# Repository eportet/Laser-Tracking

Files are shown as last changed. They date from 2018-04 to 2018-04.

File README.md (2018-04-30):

# Laser-Tracking

Code
====

Three folders in this directory:
* CameraTracking: Contains code that does corse tracking on RasPi
* Transmitter: Contains code that runs on photon plugged inito receiver PCBs
* Receiver: Contains code that runs on photon controlling servos and MEMS

Flashing Photon Code
====================

* Download Particle CLI on Mac or Linux. See Particle help for details.
* Place Photon in DFU mode by holding down both buttons, release Setup button. Light should blink purple, continue to hold the Reset button until light blinks yellow.
* Run ```particle photon compile --saveTo out.bin .``` in directory with *.ino file.
* Run ```particle flash --usb out.bin```
* When program is running, particle light should be constant white. If the light blinks green or blue, something is wrong, check that system mode is set to manual in code and that photon firmware is up to date.

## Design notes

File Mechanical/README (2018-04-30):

#Mechanical Components

Compatible with components ordered from:
[[https://www.amazon.com/gp/product/B00JXO9DBG/ref=oh_aui_detailpage_o03_s00?ie=UTF8&psc=1]]

MG995 Servos used.

Designed with Google Sketch Up.

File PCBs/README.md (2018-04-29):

# PCBs for laser tracking
We've got two PCBs to make the sensor for the drone.
The **sensor** board holds 24 photodiodes and sticks the info on a 26-pin header. The outputs require pullup resistors.
The **mux** board attaches to the sensor board, and is also designed to hold a particle photon and a RF communication module.

The kicad files, digikey bill of materials, and gerbers are in each of the directories. BOM for 3 boards + a spare, which is the minumum oshpark order.
We printed both boards with oshpark and it worked out well enough. "Sensor" is on 2oz copper, "mux" is standard.

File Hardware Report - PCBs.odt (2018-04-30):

Hardware Report

Hardware for our project includes two PCBs to be mounted on the drone. The source for these PCBs is stored in the repository, under “/PCBs/sensor” and “/PCBs/mux”.

1. Schematic files

PDFs of the circuit schematics are included in the repository, under:

1. /PCBs/sensor/sensor_sch1.pdf

2. /PCBs/sensor/sensor_sch2.pdf

3. /PCBs/mux/mux_sch1.pdf

The source files for these schematics, as well as the routed PCBs and gerber files, are included in the same directories.

2. Development Tools

We used kicad version 4.0.7 to construct these PCBs. Kicad is a free electronics design tool available on windows, mac, and linux. It can be obtained as a binary from:

http://kicad-pcb.org/

We used the standard schematic library obtained from

https://github.com/KiCad/kicad-library

The symbols for this library are intended to work with Kicad version 4.0.x. Kicad has since upgraded to version 5.0.x with new standard library components; these components are outside the scope of this document.

This library can be installed by cloning the repository, and then setting the search path to point to the cloned “/library” directory. The path can be set in:

kicad → library editor → preferences → user defined search path → add

3. Bill of materials

The bill of materials for each board is included as a CSV exported from digikey, under:

/PCBs/sensor/digikey_bom.csv

/PCBs/mux/digikey_bom.csv

Each of these BOMs represents the components needed for one board without spares. It is recommended that when you purchase components, you buy slightly more than necessary to account for damaged or lost components during manufacturing. The OSHPark minimum board order is three copies of a board; we generally ordered parts for four.

Datasheets for these parts are available from digikey.

4. Power

Our boards are designed for a 5-volt power source, which will also power the particle photon and the NRF24L01 module when they are connected. The five volt input should be connected to each board on the pins in positions marked with the red circle below. The adjacent pin is the ground pin.

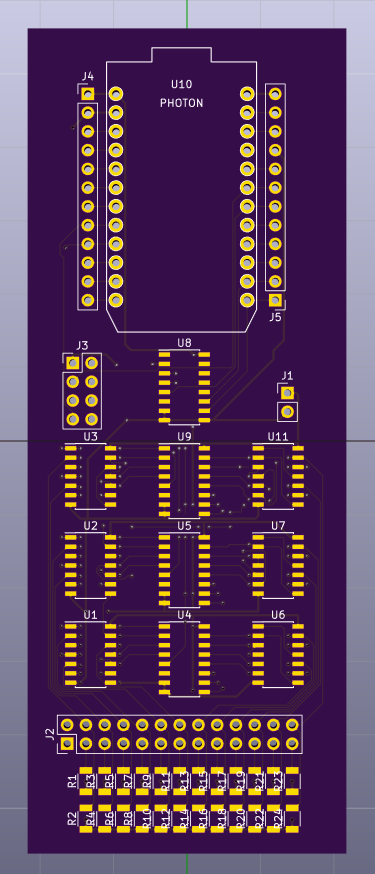
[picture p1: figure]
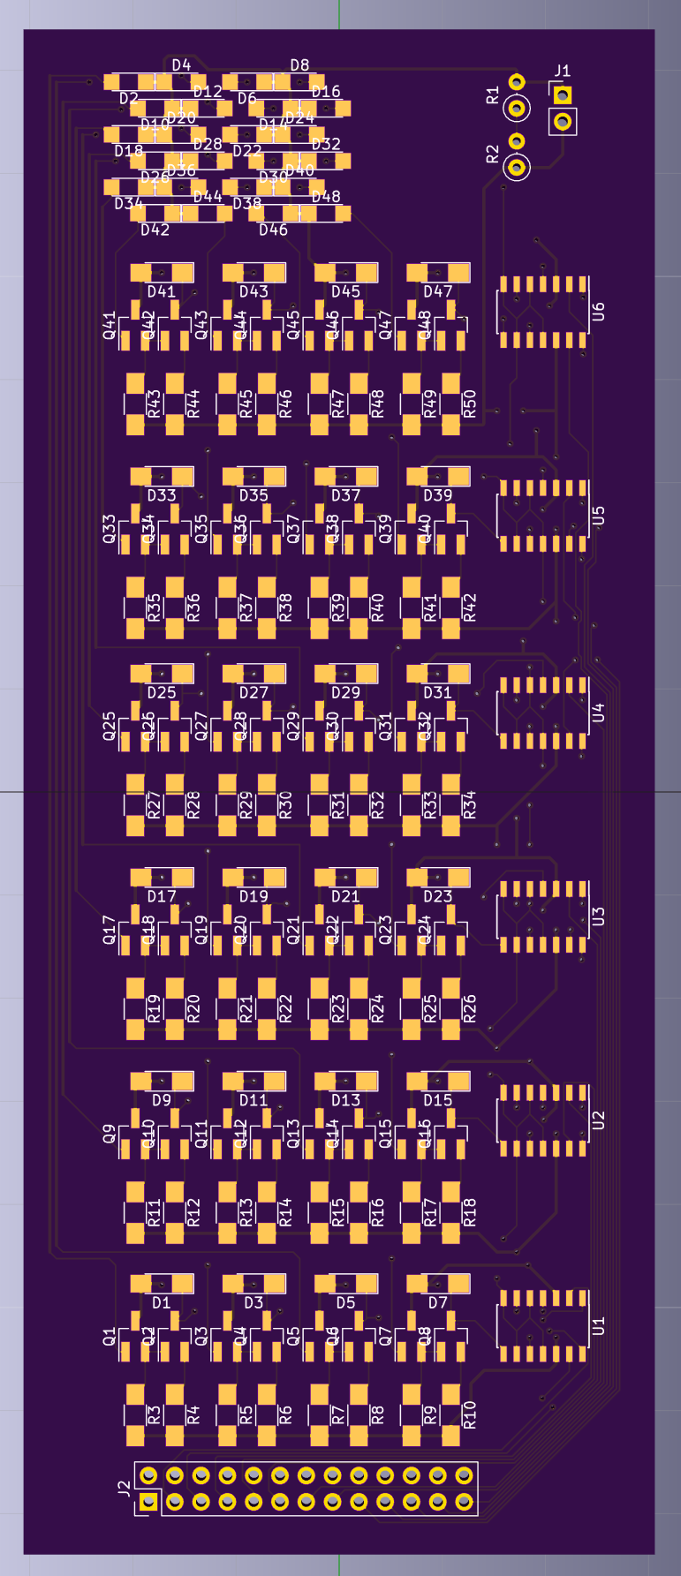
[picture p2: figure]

The “Sensor” board (left) has a resistor bridge next to the power input, designed to be filled with through-hole resistors. This bridge sets the sensitivity threshold of the photodiodes. The ratio of r2 / r1 should be about 3/2. Raising the value of r2 will decrease the sensitivity of the resistors, and lowering it will do the opposite.

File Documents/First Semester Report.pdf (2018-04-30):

## Boston University Electrical & Computer Engineering

EC 463 Capstone Senior Design Project

## First Semester Report

## UAV Laser Tracking

Submitted to

Professor Thomas Little, PhD 8 St. Mary’s St., Boston
MA 02215, Room 426
(617) 353-9877
tdcl@bu.edu

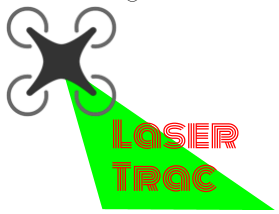
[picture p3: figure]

by Team 15
LaserTrac

Team Members
Aviva Englander | englanda@bu.edu
Christopher Liao | cliao25@bu.edu
Jeffrey Lin | jlin96@bu.edu
Anton Paquin | paquin@bu.edu
Eduardo Portet | eportet@bu.edu

Submitted: 12/11/2017

First Semester Report | 1

Table of Contents

Executive Summary | 2
1. | Introduction | 3
2. | Concept Development | 4
2.1. | Laser Steering Mechanism | 5
2.2. | Receiver | 6
2.3. | Tracking Algorithm | 7
2.4. | Backlink | 7
3. | System Description | 8
3.1. | Backwards Link | 8
3.2. | Primary Station Controller | 8
3.3. | Laser Controller | 9
3.4. | Data Controller and Laser | 9
3.5. | Photodiode Array | 9
3.6. | Motion Controls | 10
3.7. | Camera and Coarse Control | 10
4. | First Semester Progress | 11
5. | Technical Plan | 12
5.1. | Establish Backwards Link | 12
5.2. | Build Servo Control | 12
5.3. | Build MEMS Control | 12
5.4. | Tracking Algorithm | 13
5.5. | Second Deliverable Testing | 14
5.6. | PCB Design | 14
5.7. | Tracking Algorithm Testing | 14
5.8. | Minimum Deliverable by Functional Testing | 15
6. | Budget Estimate | 15
7. | Attachments | 16
7.1. | Engineering Requirements | 16
7.2. | Gantt Chart | 16
7.3. | Photodiode Circuit | 17
7.4. | Stepper Motor Circuit | 18
7.5. | Tracking Algorithm Block Diagram | 18
7.6. | Receiver Block Diagram | 19
Team 15 - Laser Tracking | 12/11/2017

Executive Summary

Laser tracking and Communication with UAVs Team 15 -LaserTrac

As the radio spectrum becomes more crowded, interference has become an increasingly urgent problem. Wireless Optical Communication (WOC) has emerged as an attractive alternative to radio communication, since it can be aimed at a specific point. Currently WOC is used between stationary objects in many cities, where the transmitter is often mounted on top of skyscrapers to ensure clear line-of-sight. However, WOC with moving targets is still being researched.

The goal of our project is to maintain two-way WOC with an Unmanned Aerial Vehicle (UAV). In order to accomplish this goal, the problem of tracking a moving object must be solved. We intend to use the laser used for communication to track the UAV. While both WOC and laser tracking are well researched, there is little prior work focused on accomplishing both communication and tracking with one laser device. Potential applications for our project include providing internet access to disaster areas, drone racing, and air traffic control.

### 1. Introduction

Currently the radio frequency spectrum is cluttered and requires a license for use. We want to develop a method of rapid data transmission which doesn’t require a license. What differentiates optical communications from radio frequency communications is its “high data rate capabilities and ultra dense access point deployment” (Rahaim and Little 2017). Free space optical communications can potentially transmit data at rates of up to Gbps (Hyperion Project). Which is why optical wireless communication will be a viable alternative to radio frequency communications.

The paramount issue with using wireless optical communications with moving aerial vehicles is there is no good way to keep the visible light focused on the vehicle. Without our project this communication link cannot be maintained for moving aerial vehicles resulting in gaps in communication and lost data.

Our laser tracking system has many applications. It can be used to provide Wi-Fi in remote areas and to communicate with planes in crowded airfields where the RF spectrum is extremely crowded. In addition it will be useful in drone racing scenarios for providing remote control.

Our project’s goal is to maintain a constant communication link with aerial vehicles. Our laser tracking system can be used for any kind of rapid information transmission from a ground station to fast-moving aerial vehicles.

### 2. Concept Development

The problem presented by our client was very general: Professor Little wants technology that can track a fast moving object in three dimensions with a laser beam. While there are numerous useful application for this technology, we and the client have agreed to narrow the scope of the project to a drone racing scenario to reduce ambiguity and facilitate development of engineering objectives. Figure 2.1 illustrates the initial visualization provided by the client. As a drone moves to the right, the base station follows the quadcopter to the right with a laser. The quadcopter also has a laser backlink aimed at the base station. This backlink would presumably have to be a different wavelength (a green laser instead of a red laser for example). After discussion with the client, we made the optical backlink optional due to time constraints.

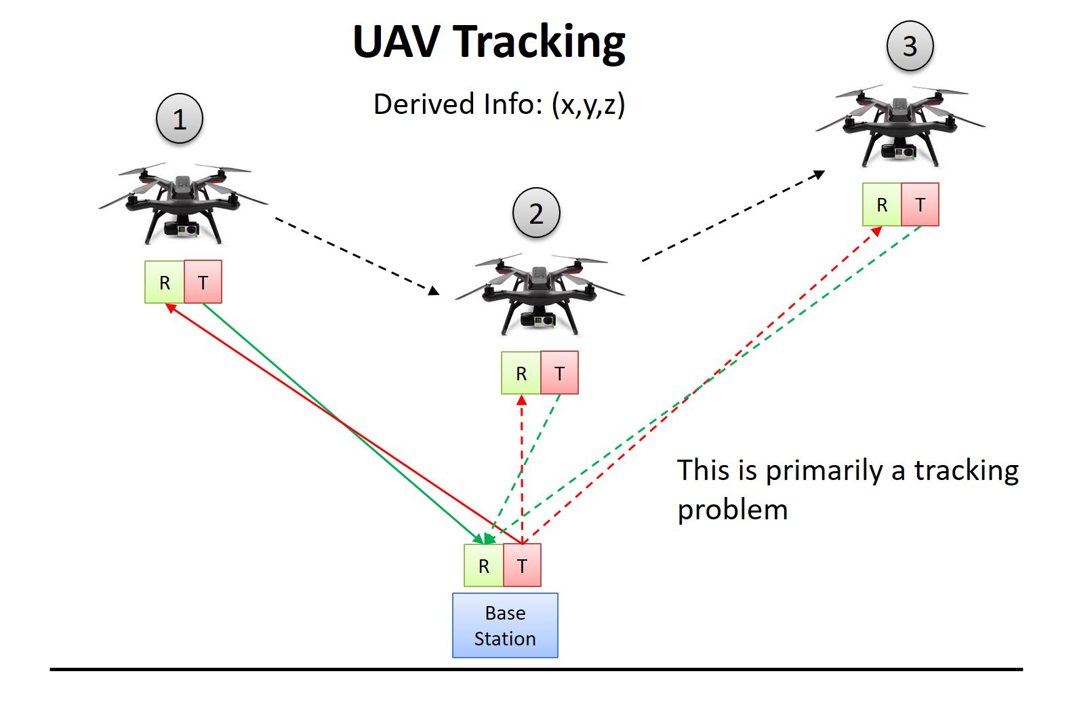
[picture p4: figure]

Figure 2.1. Visualization of Laser Tracking
From the initial discussion with the client, we came up with the following concept. The laser steering mechanism would be implemented using a MEMS mirror. The advantage of a MEMS mirror is threefold: 1) it can rotate at up to 4 kHz and thus can quickly acquire signal from the drone’s receiver, 2) it is precise, which makes tracking of far-away objects viable, 3) unlike any servo system made of motors, the mirror has negligible inertia, allowing high acceleration. The MEMS mirror setup was already provided by the client. The setup consists of a laser beam routed through optical fiber and aimed at the MEMS mirror. Currently the laser’s line of sight is constrained by the bracket holding it. For the final design, we will have to modify the mount of the laser and the MEMS mirror so that the laser can be aimed anywhere above the horizontal plane. The client emphasized that the drone itself is not a deliverable for the project.

We are only responsible for delivering the receiver, but a drone will be provided for testing. The receiver assembly and tracking method are the two most important design decisions we have to make. The initial concept for the receiver was an array of photodiodes on a circuit board. The tracking algorithm will be a form of feedback control. We agreed that the final control
mechanism must be closed loop, but the client has IR positioning equipment available for testing. The initial tracking algorithm built off of the following simple scenario. Assume that the receiver consists of two photodiodes and is constrained to move along a line. When the laser hits the left photodiode, it laser is moved right and vice versa. Using this rudimentary tracking algorithm, we would theoretically be able to track the receiver regardless of its motion assuming that the motor can accelerate at any rate and move at any speed and that there is no latency in the feedback signal. This rudimentary tracking method was the starting point for development of a tracking algorithm.

Given the complexity of this project, we chose a divide-and-conquer approach to concept development. We focused on designing one component at a time. The following paragraphs go into more detail about development of each component.

### 2.1. Laser steering mechanism

We went back and forth between using the MEMS mirror provided and a servo mechanism for steering. The advantage of the MEMS mechanism has already been discussed above. The advantages of the servo mechanism is that it is cheaper and more rugged. Motors are also more intuitive to control and may be easier to debug. Adding the MEMS mirror adds another layer of complexity. Right now, we are working on getting the MEMS mirror working and building a stepper motor mechanism in parallel. If we can get the MEMS mirror working, work on building the servo mechanism isn’t necessarily in vain, since we have plans to mount a RasPi camera on the servo for coarse tracking (more on this in following sections). The mirror steers the beam by tilting the mirror in different directions. The tilt of the motor is controlled by a voltage in the x direction and a voltage in the y direction. However, the tilt of the angle does not correspond directly with the position of the drone. We will need to write a function that takes the polar coordinates of the drone as input and outputs the tilt of the mirror in the x and y directions, taking into account the angle at which the laser beam is incident. The stepper motor assembly is slightly easier to control, because we can move the laser into position based on a set of polar coordinates.

### 2.2. Receiver

We agreed in the beginning that the receiver would consist of an array of photodiodes, the design of the photodiode array has changed over the semester. Theoretically, if there were no limits on the laser steering mechanism, and we are able to obtain an analog value from the photodiodes, we could build a receiver with four photodiodes and design a tracking mechanism using PID control. Such a receiver would have a photodiode in the middle to demodulate the laser (for communication). The other four diodes would be positioned in each of the four coordinate directions. In this setup, we would assume that the photodiode is able to output an analog value based on the distance the laser is from the photodiode. For example, if the laser is left-of-center, as the beam moves away from the center photodiode and closer to the left photodiode, the intensity of light the left photodiode sees would increase, and thus its analog value would increase. The analog value outputted by each of the four photodiodes could be used as the error function in the PID control loop. There are two main problems with this solution:

- The photodiode connected in reverse bias configuration can output a analog value, but since it quickly deflects to extremes, it is as good as a digital signal.
- Transmitting the analog signal takes longer, and latency is a critical factor in feedback control loops.

The concept that we settled on is a 4x4 array of photodiodes. Each photodiode would output a digital value. The feedback would consist of 4 bits indicating the photodiode that is on. For this to work, the photodiodes must be close enough to each other that the laser beam can’t slip between adjacent diodes. More specifically, the beamwidth of the laser must never be less than the distance between adjacent photodiodes. The disadvantage of this design is that we can only resolve the position of the laser relative to the center of the receiver down to the distance between the photodiodes. This gives us a very imprecise error function and thus puts a lot of burden on the tracking algorithm.

### 2.3. Tracking Algorithm

For the tracking algorithm, we decided to use video processing from a RasPi camera to get initial coarse positioning. To make our video processing algorithm robust in situations with multiple moving overhead objects, we decided to add a pattern of leds to the bottom of the drone. Having an easily identifiable pattern will make identifying our drone easier.

For the fine positioning we plan on using a feedback loop with predictive tracking. The ground station will get its initial pointing positioning from the video processing unit and will point in that area until it gets feedback from the drone telling it which way to move. The drone will have a photodiode array, which it will read with an Arduino Leonardo in order to determine which direction the laser will need to move to hit the center photodiode. This information will be transmitted back to the ground station using radio frequency transmitters. Then the laser will move in the direction directed by the signal from the drone. When the laser hits the center photodiode, the azimuth and elevation angles will be used as measurements to update the Kalman filter and to predict where the laser should point next.

### 2.4. Backlink

As mentioned already, communication back from the drone using laser is optional. Judging from the progress so far, it seems unlikely that this will be a wireless optical link. We will use radio communication instead. The bitrate of this link is critical, since it is the feedback for tracking. We have previously considered using Bluetooth for this, since we have experience with Bluetooth. We decided that Bluetooth is too slow for this application. We have purchased NRF24L01 transceivers. These transceivers are cheap and compatible with Arduinos. The transmission bandwidth and the range are also suitable for our application.

### 3. System Description

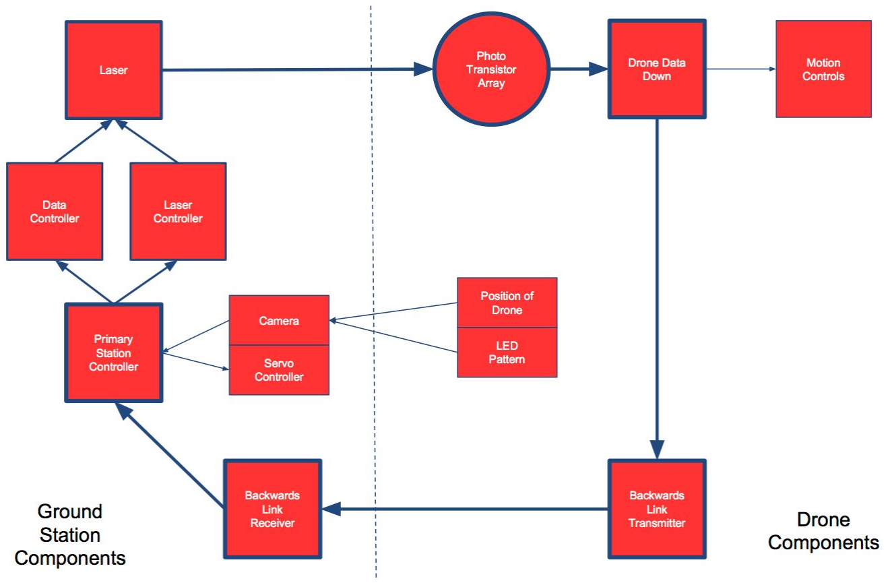
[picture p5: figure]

Figure 3.1. Block Diagram for System

The system diagram above shows the major components in our design. The bolded path represents the critical path we have to build in order to have the bare minimum on ECE Day. The other parts are optional. In this section, the critical components will be developed, then the optional components.

### 3.1. Backwards link

The backwards link will use radio communication. The bandwidth of the backlink is critical. We will use nRF24L01, which can communicate up to 2 mbps. This transceiver communicates with the Arduino through SPI. At the drone end, there will be an Arduino which takes input from the photodiode array (4 bits in parallel) and outputs it to the transceiver using SPI interface. The base station’s “Primary Station Controller” will receive data from the radio transceiver on the ground through SPI. The nRF24L01 has capabilities of communicating at 2 Mbps which is more than enough for our customer’s requirement of 250 Kbps.

### 3.2. Primary Station Controller

The station controller will be a RasPi. This will be where the tracking algorithm lives. The tracking algorithm will take the 4 bit feedback from the RF transceiver as input and output signals to the laser and servo controllers. From the 4 bits transmitted by the drone’s photodiode array, the tracking algorithm can determine how off centered the laser beam is from the center of the array. Using this information, the Kalman Filter will update its model of the drone’s trajectory and predict the drone’s position and speed at the next time step. This information is passed to both the laser controller and the servo controller. The specifics of the Kalman Filter will be discussed in Section 5.

### 3.3. Laser Controller

The Laser Controller will be an Arduino. The job of the laser controller is to take the position prediction from the Kalman Filter as input and output control signals to the laser steering mechanism. Using the position (given in rectangular coordinates), the polar coordinates (angle, pitch and distance) are calculated. If the laser were mounted on a servo mechanism with two stepper motors, this information can be inputted directly into the motor controllers. If the laser is steered using the MEMs mirror, another function must convert the position vector in polar coordinates to degree of tilt (of the mirror) with respect the x and y axis. This function is also a function of the angle of incidence of the laser on the mirror (which is constant).

### 3.4. Data Controller and Laser

This is the simplest part of the critical loop. The Laser will be modulated using on/off keying. The data controller will turn the laser on and off using the the UART hardware in the Arduino. From the Data Controller’s perspective, this is no different than sending Serial communication over a wired connection.

### 3.5. Photodiode Array

The photodiode array is an array of 4x4 photodiodes. We may expand to 5x5 or even 6x6 next semester. The output of the Photodiode array circuit is a four bit number corresponding to the position of the photodiode that sees the highest intensity of light. The laser beam will most likely turn on multiple photodiodes, since the width of the laser beam will be larger than the distance between adjacent photodiodes by design. We will build a winner-takes-all circuit that will output the 4 bit value of the photodiode seeing the highest intensity from the laser, which will best approximate the location of the laser beam’s center.

Aside from tracking, the photodiode array also has to demodulate the message encoded in the laser beam. For this, each of the photodiodes must also output a digital value (using the circuit in Appendix), and connected to an OR gate. The OR gate’s output is the data downlink.

### 3.6. Motion Controls

Using the current setup, the sole purpose of the laser is to communicate data to the drone. Nothing is done with that data. In an application such as drone racing, this data will likely be used to control the drone. If we are able to complete the critical loop, we will try to control a drone using data transmitted by the laser. To do this, we must build our own drone from scratch. Once finished, we would need to connect the data output from the photodiode array to the Rx pin of the flight controller.

### 3.7. Camera and Coarse Control

Currently, we must assume that the laser is initially aimed at the receiver array, and that the laser never loses track of the drone during flight. This is an unrealistic assumption, and we must have a way to acquire the rough position of the drone. We will do this with a RasPi camera mounted on a servo. There will be an LED pattern mounted on the drone’s receiver that the camera will look for.

### 4. First Semester Progress

In our first semester, we wanted to create minimum viable products for each major component and connection of the critical path shown in the system diagram. For our first round of deliverable testing, we came up with two essential tests for our product. The objective of our first test is to showcase the communication aspect of our project. Since the purpose of the project is to maintain laser communication with a moving target, establishing laser communication is an integral part. A successful test demonstrates that the receptor circuit and laser modulation mechanism work as intended. Our product relies on a closed loop system and the communication between the ground station and the drone is one of the most important components. Once we achieve this first objective, we can focus on the more difficult problem at hand, our tracking mechanism.

Tracking is the second of our two main problems in this project, and also the more difficult. While the tracking setup demonstrated during the test is simple, it is a good baseline to build more sophisticated tracking mechanisms upon. This test demonstrates our ability to control the laser with a servo and to maintain a feedback loop between the receiver and transmitter using a linear photodiode array. The tracking test was very constricted by the lack of equipment to measure distance and positioning of the laser to the photodiode array. However, we managed to demonstrate that the laser would lose sight of the photodiodes within a distance of 20cm, which doesn’t even reach the minimum requirement for the operating range.

Past the first deliverable testing, we have built the 4x4 photodiode array and initiated testing of a tracking algorithm for a two dimensional space. This is a crucial step in the course of the project that will require a lot of time to develop and debug. We have also managed to control the MEMS mirror to point the laser to the locations we desire. We still need to fully test the capabilities of the mirror, and identify how small of a change in position it can achieve to increase precision of the laser at longer distances. In this manner we can reach a decision regarding the use of a stepper motor or the MEMS mirror.

### 5. Technical Plan

### 5.1 Establish Backwards Link

Establish a radio link from the receiver to the base station. This link will use the RF transmitters already purchased. They will interface with Arduinos using SPI. The transmission will be 4 serial bits. The four bits are outputted by the photodiode array circuit to indicate the position of the photodiode that is on. Design considerations that need to be ironed out include the following:

- Time between transmissions.
- Transmission rate. Nominal maximum rate is 2 Mbps, but this may be higher than what we can achieve in reality.

### 5.2 Build Servo Control

This part includes linking the stepper motors with drivers and testing to make sure the stepper motors are able to move at a speed specified and to a position specified to a certain degree of precision. The precision needed has already been calculated, and the components have already been chosen accordingly. The main task remaining is the physical assembly (including 3D printing a bracket) and wiring everything up.

Back-end functions need to be written to interface between the tracking algorithm and the motors. This may include setting up the timer counter in the Arduino to control the step frequency of the motor.

### 5.3 Build MEMS Control

There are three main tasks to this part: 1) setting up the MEMS mirror 2) writing the polar coordinates-to-tilt function, and 3) physical mounting.

Task 1: This is partly done. The deliverable outcome of this task is to output x and y tilt to the mirror and verifying that the mirror tilts to the correct angle. For example, if the laser beam shines vertically down on the mirror and the mirror is tilted 45 degrees, then the laser should be reflected horizontally. A function should be written that takes two inputs -- tilt in y direction and tilt in x direction -- and outputs the appropriate signals to the MEMS mirror.

Task 2: We need to write a function that takes polar coordinates as input and outputs the tilt of mirror in x and y directions. The angle of incidence of the laser on the mirror is fixed and should be taken as a constant parameter. This part mainly involves doing some basic trigonometry to figure out the relations.

Task 3: The bracket that the MEMS mirror is currently mounted on heavily constrains its line-of-sight. More specifically, the MEMS mirror is set back from the aperture and cannot see from 30 degrees above the horizon. We will need to mount the MEMS mirror so that it can “see” the horizon. We also need to determine the optimal angle of incidence of the laser, and mount the laser in a way that minimizes the blind spot created by the laser.

### 5.4 Tracking Algorithm

The tracking Algorithm is divided into two separate tasks: Theory and implementation. The deliverable of the theory stage is detailed pseudocode for the Kalman Filter. Implementation involves converting the pseudo code into functional C code. The theory part can be broken down into more parts as follows.

Task 1: Defining a model for the drone’s trajectory. As an example, the most obvious way to model a trajectory is using position, acceleration and velocity vectors. Using this model, the Kalman Filter must store three vector values (nine scalar values). The Kalman Filter must output the predicted position to the MEMS or Servo Controller at regular time intervals, which needs to be decided upon. This time interval should be relatively small (~ 1 ms) to avoid jerky movement.

Task 2: Defining the update function for the Kalman Filter. This is somewhat more complicated than the first task. This function will be called every time the 4 error bits are received from the drone’s receiver. As an example, if a receiver starts from rest, the Kalman Filter models the position as x(t) = 0. When the receiver moves up and the error becomes -1, then the Kalman Filter might change to x(t) = t.

Task 3: Making the Kalman Filter more robust. At this stage, the Kalman Filter should work under normal conditions. However, edge cases need to be handled. For example, if the receiver is moved up, turned 180 degrees, and then moved back down, the tracking algorithm might not know that the receiver turned and thus continue moving up.

Task 4: Implement the Coordinate transform function. Convert Rectangular Coordinates to Polar Coordinates. This is trivial, but note that we may find it easier in the end to use an alternate coordinate system.

### 5.5 Second Deliverables Testing

At this stage, we plan to deliver the following.

- A receiver which is able to receive data at the data rate specified by the Engineering Requirements.
- A tracking algorithm which is able to track the receiver provided that its orientation does not change.
- The receiver circuit should be finished and the feedback loop functional.
- Either MEMS mirror or servos to steer the laser.

Given that the receiver remains in the same orientation, the laser should track the receiver as it is moved up to 10 m/s and accelerated up to the acceleration due to gravity. We will demonstrate this by holding the receiver in front of the laser and moving it in an unpredictable manner.

### 5.6 PCB Design

Design a PCB for the receiver and have it shipped by at least two weeks before functional testing. The design of the PCB will depend upon the circuit from previous tasks. The photodiode array will probably by 5x5 or 6x6.

### 5.7 Tracking Algorithm Testing

This will be the least straight forward task for next semester. Many of the details depend upon development of the tracking algorithm up to this point. This is where we must address the cases where the tracking algorithm fails and attempt to address the issue. Foreseeable problems that need to be addressed at this stage include:

- Changing orientation of the receiver
- Tilting the receiver away from the laser
- Momentary loss of signal from the receiver (less important)

An acceptable deliverable from this task will have solved the first two bullet points above by functional testing week.

### 5.8 Minimum Deliverable by Functional Testing

Redo the test from previous testing with two complications. We can change the orientation of the receiver and tilt it. At this point, we may try to mount the receiver on a drone. However, going from holding the receiver in hand to mounting it on a drone is not difficult. It can be argued that following a hand is much more difficult than following a drone, since a drone’s trajectory is more predictable. However, tracking a drone looks cooler.

### 6. Budget Estimate

For this project, there were no items that would constrain our budget that were not already provided to us. Our customer provided us with the expensive technologies such as the drone and the MEMS micromirror, and also some small microcontrollers. Most of the parts that we had to cover through the budget were components that we used to build the tracking system and receiver device that goes on the drone. We have already obtained the items that will be most crucial for the completion of this project, so the addition to this list will be minimal and of no significant cost.

Item 1 | Description Laser Diodes (10) | Cost $2.59
2 | Raspberry Pi 3 | $40.00
3 | Arduino Leonardo (2) * | $39.60
4 | Photodiodes (25) | $16.69
5 | RF Transmitters/Receivers | $11.98
6 | Raspberry Pi Camera Module V2 | $22.99
7 | Stepper Motor Driver DRV8825 | $11.59
8 | Stepper Motor NEMA 17 (2) | $23.98
9 | 4 Quadrant Actuator MEMS A1M16.5 Micromirror * | $499.00
10 | DJI Phantom 4 Drone * | $1,199.00
| Total Cost | $1,867.42
*Provided by customer

### 7. Attachments 7.1. Appendix 1 – Engineering Requirements

Requirement Optical beam type | Value, range, tolerance, units Class 1 or Class 1M
Weight of receiver on drone | ≤ 100 grams
Battery powering receiver on drone | ~ 10mW
Coarse position of drone acquired | 5 seconds
Fine position of drone acquired | 1 second
Range of operation | 1 - 20 meters
Tracking speed | 10 m/s or 36 km/h
Data rate to receiver | ≥ 250 Kb/s

### 7.2. Appendix 2 – Gantt Chart

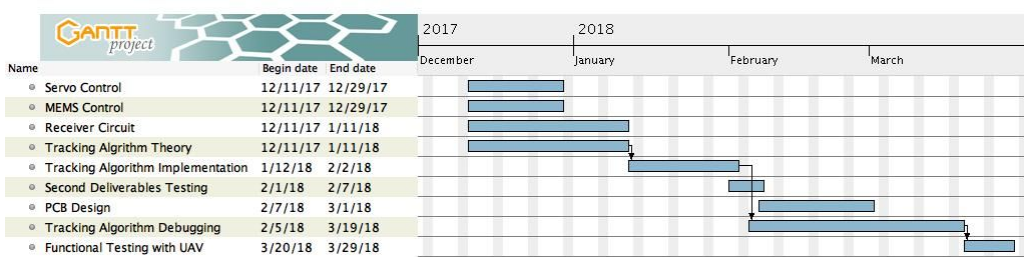
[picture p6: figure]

### 7.3. Appendix 3 – Photodiode Circuit

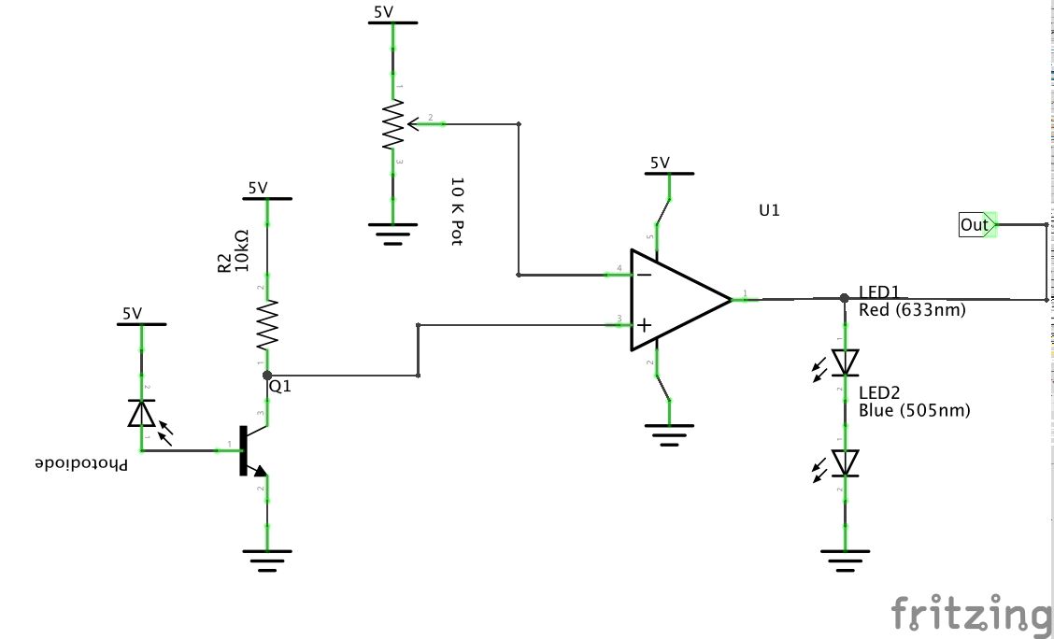
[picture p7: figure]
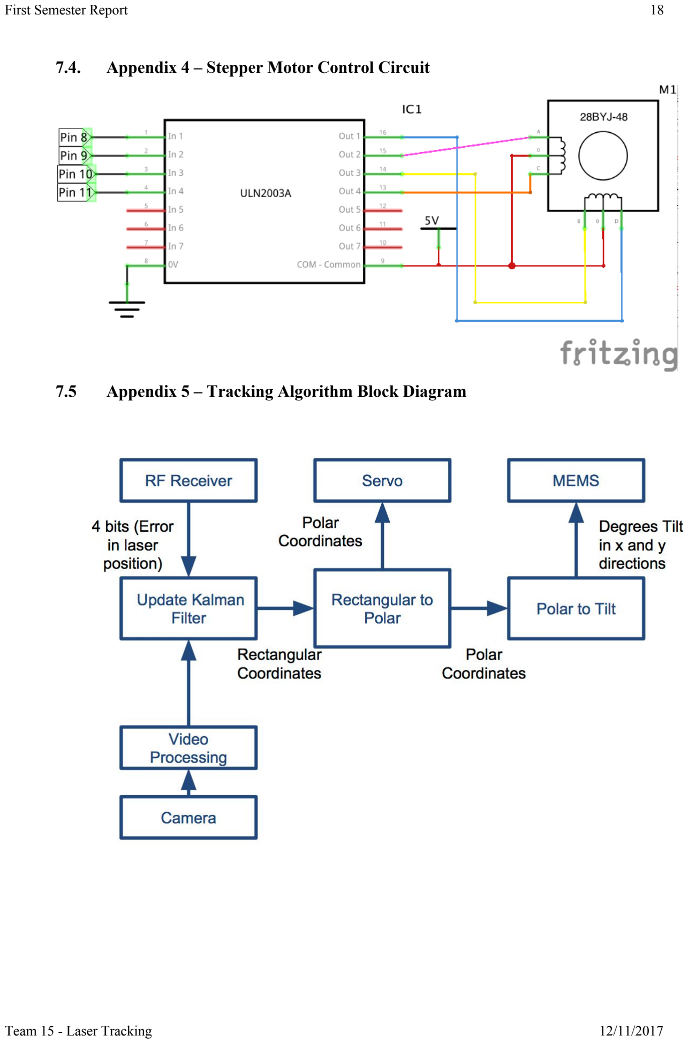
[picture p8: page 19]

### 7.4. Appendix 4 – Stepper Motor Control Circuit

### 7.5 Appendix 5 – Tracking Algorithm Block Diagram

### 7.6 Appendix 6 – Receiver Block Diagram

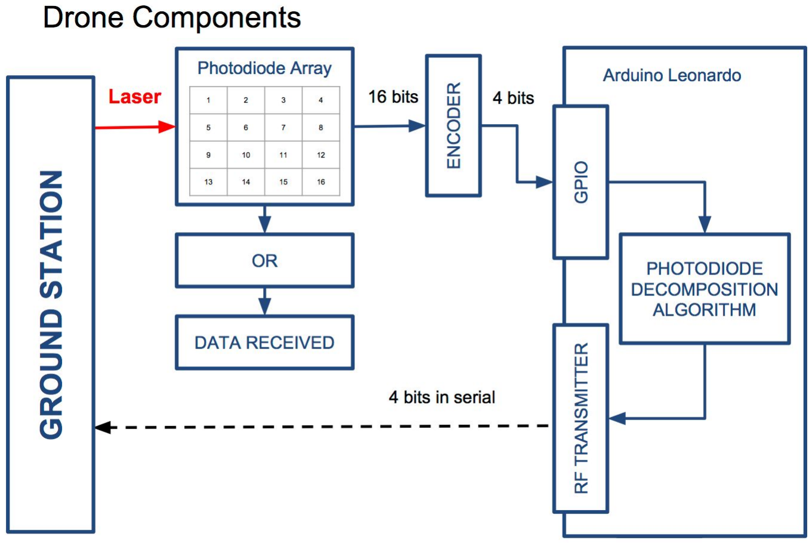
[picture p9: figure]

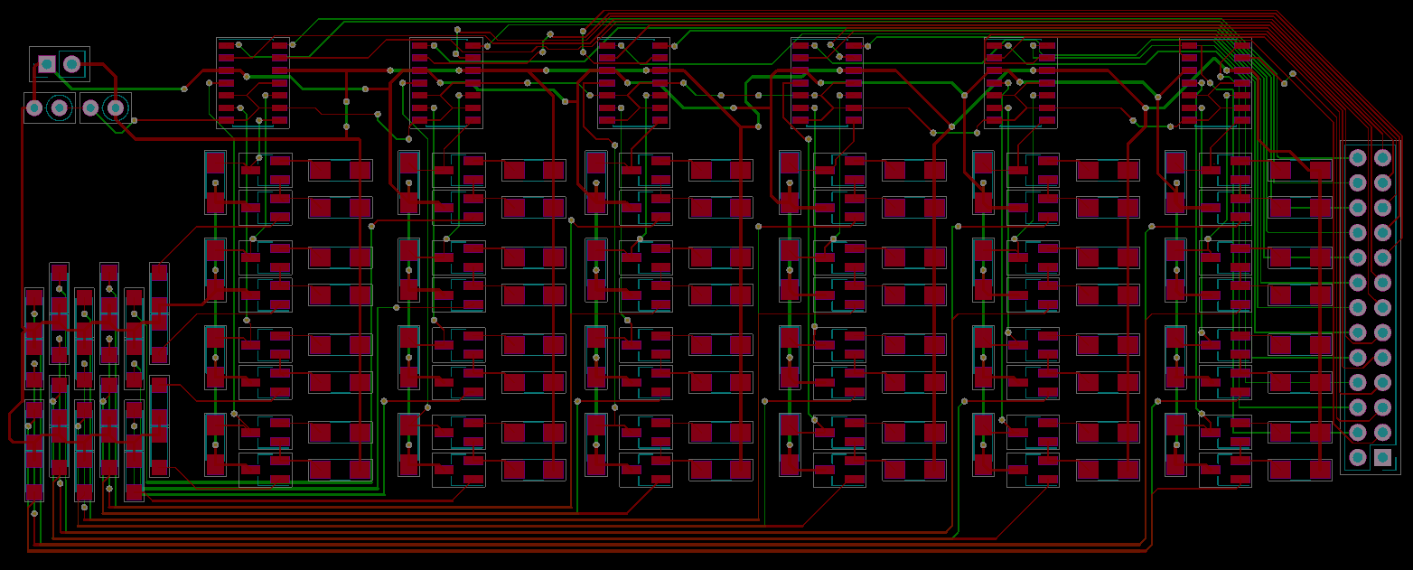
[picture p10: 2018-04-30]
PCBs/sensor/layout.png

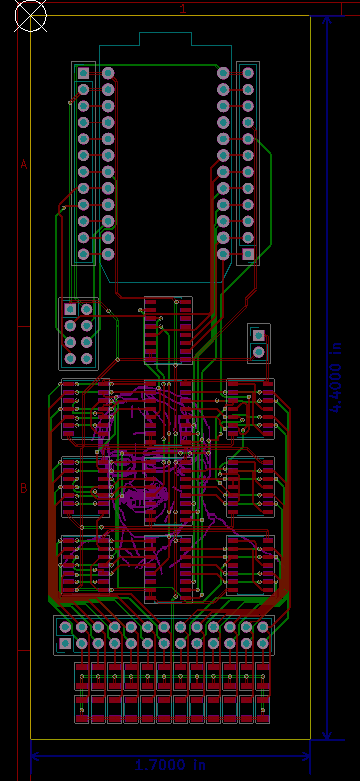
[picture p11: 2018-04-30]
PCBs/mux/layout.png

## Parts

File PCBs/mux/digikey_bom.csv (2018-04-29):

Manufacturer Part Number | Manufacturer | Digi-Key Part Number | Customer Reference | Reference Designator | Packaging | Part Status | Quantity | Unit Price | Extended Price | Quantity Available | Mfg Std Lead Time | Description | RoHS Status | Lead Free Status | REACH Status
74HC32D,652 | Nexperia USA Inc. | 1727-3786-ND |  |  | Tube | Active | 6 | 0.35000 | $2.10 | 1721 | 8 Weeks | IC GATE OR 4CH 2-INP 14-SO | RoHS Compliant | Lead free | REACH Unaffected
74HC151D,653 | Nexperia USA Inc. | 1727-7294-1-ND |  |  | Cut Tape (CT) | Active | 4 | 0.42000 | $1.68 | 4283 | 8 Weeks | IC MUX 8-INPUT 16SOIC | RoHS Compliant | Lead free | REACH Unaffected
61300211121 | Wurth Electronics Inc. | 732-5315-ND |  |  | Bag | Active | 1 | 0.13000 | $0.13 | 82895 | 13 Weeks | CONN HEADER 2 POS 2.54 | RoHS Compliant | Lead free | REACH Unaffected
SBH11-PBPC-D13-ST-BK | Sullins Connector Solutions | S9173-ND |  |  | Tray | Active | 1 | 0.66000 | $0.66 | 9694 | 4 Weeks | CONN HEADER 2.54MM 26POS GOLD | RoHS Compliant | Lead free | REACH Unaffected
RC1206FR-0768KL | Yageo | 311-68.0KFRCT-ND |  |  | Cut Tape (CT) | Active | 24 | 0.03300 | $0.79 | 3982 | 23 Weeks | RES SMD 68K OHM 1% 1/4W 1206 | RoHS Compliant | Lead free | REACH Unaffected
PPTC121LFBN-RC | Sullins Connector Solutions | S6100-ND |  |  | Tray | Active | 4 | 0.78000 | $3.12 | 10754 | 4 Weeks | CONN HEADER FEM 12POS.1" SGL TIN | RoHS Compliant | Lead free | REACH Unaffected
PPTC042LFBN-RC | Sullins Connector Solutions | S7072-ND |  |  | Tray | Active | 1 | 0.67000 | $0.67 | 5109 | 4 Weeks | CONN HEADER FMALE 8PS .1" DL TIN | RoHS Compliant | Lead free | REACH Unaffected

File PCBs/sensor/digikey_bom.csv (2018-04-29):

Manufacturer Part Number | Manufacturer | Digi-Key Part Number | Customer Reference | Reference Designator | Packaging | Part Status | Quantity | Unit Price | Extended Price | Quantity Available | Mfg Std Lead Time | Description | RoHS Status | Lead Free Status | REACH Status
SFH11-PBPC-D13-ST-BK | Sullins Connector Solutions | S9198-ND |  |  | Tray | Active | 1 | 1.39000 | $1.39 | 3976 | 4 Weeks | CONN HEADR FMALE 26POS .1" DL AU | RoHS Compliant | Lead free | REACH Unaffected
SFH 2701 | OSRAM Opto Semiconductors Inc. | 475-2967-1-ND |  |  | Cut Tape (CT) | Active | 25 | 0.66760 | $16.69 | 2066 | 14 Weeks | PHOTODIODE PIN 820NM SMD | RoHS Compliant | Lead free | REACH Unaffected
PPTC021LFBN-RC | Sullins Connector Solutions | S7000-ND |  |  | Tray | Active | 1 | 0.32000 | $0.32 | 27573 | 4 Weeks | CONN HEADER FEMALE 2POS .1" TIN | RoHS Compliant | Lead free | REACH Unaffected
LTST-C150KRKT | Lite-On Inc. | 160-1405-1-ND |  |  | Cut Tape (CT) | Active | 25 | 0.20720 | $5.18 | 104786 | 14 Weeks | LED RED CLEAR 1206 SMD | RoHS Compliant | Lead free | Not Available
CF14JT10K0 | Stackpole Electronics Inc. | CF14JT10K0CT-ND |  |  | Cut Tape (CT) | Active | 2 | 0.10000 | $0.20 | 875576 | 14 Weeks | RES 10K OHM 1/4W 5% AXIAL | RoHS Compliant | Lead free | REACH Unaffected
RC1206JR-0768RL | Yageo | 311-68ERCT-ND |  |  | Cut Tape (CT) | Active | 25 | 0.02500 | $0.62 | 331576 | 23 Weeks | RES SMD 68 OHM 5% 1/4W 1206 | RoHS Compliant | Lead free | REACH Unaffected
RC1206JR-0710KL | Yageo | 311-10KERCT-ND |  |  | Cut Tape (CT) | Active | 25 | 0.02500 | $0.62 | 787292 | 23 Weeks | RES SMD 10K OHM 5% 1/4W 1206 | RoHS Compliant | Lead free | REACH Unaffected
LM339DT | STMicroelectronics | 497-1588-1-ND |  |  | Cut Tape (CT) | Active | 7 | 0.46000 | $3.22 | 3951 | 38 Weeks | IC COMPARATOR LP QUAD 14-SOIC | RoHS Compliant | Lead free | Not Available
MMBT3904-7-F | Diodes Incorporated | MMBT3904-FDICT-ND |  |  | Cut Tape (CT) | Active | 50 | 0.11900 | $5.95 | 0 | Not Available | TRANS NPN 40V 0.2A SMD SOT23-3 | RoHS Compliant | Lead free | REACH Unaffected

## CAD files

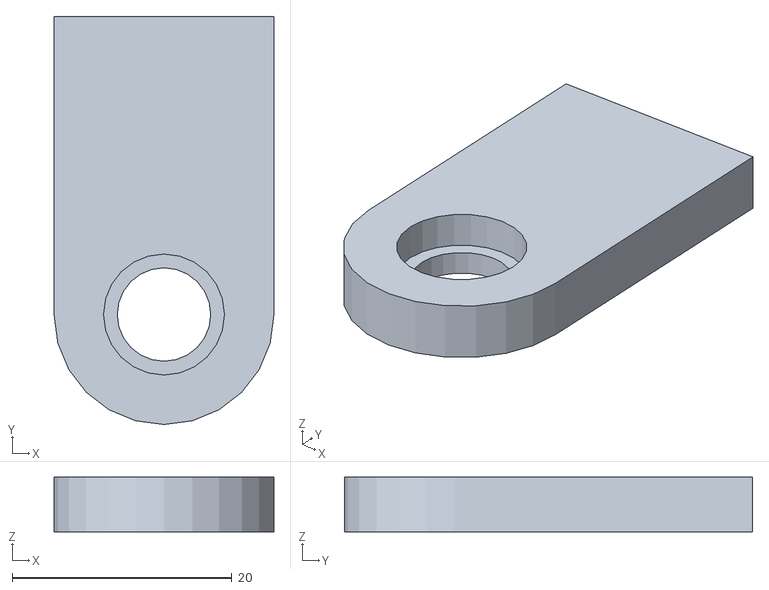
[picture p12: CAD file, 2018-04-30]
Mechanical/left_pivot.stl
20.0 x 37.1 x 5.00

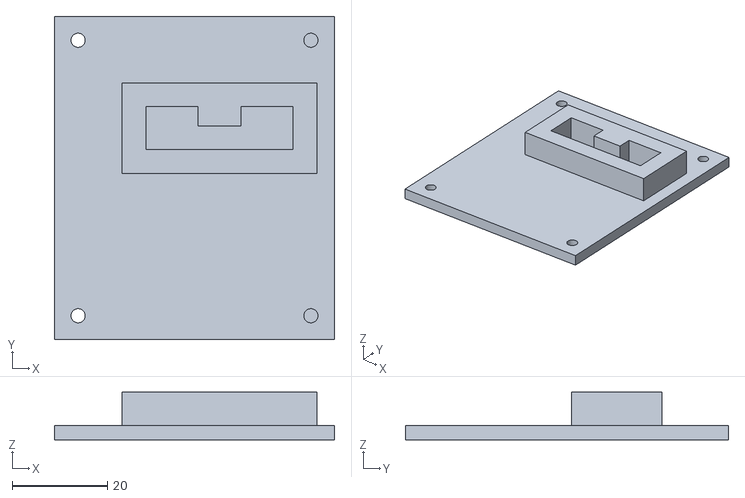
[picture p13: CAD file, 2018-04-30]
Mechanical/raspi_mount.stl
59.0 x 68.0 x 10.0

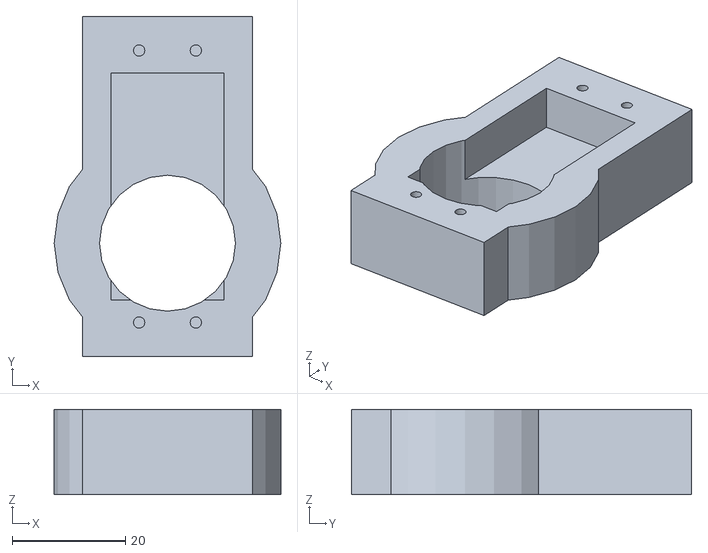
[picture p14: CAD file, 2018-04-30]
Mechanical/servo bracket.stl
40.0 x 60.0 x 15.0

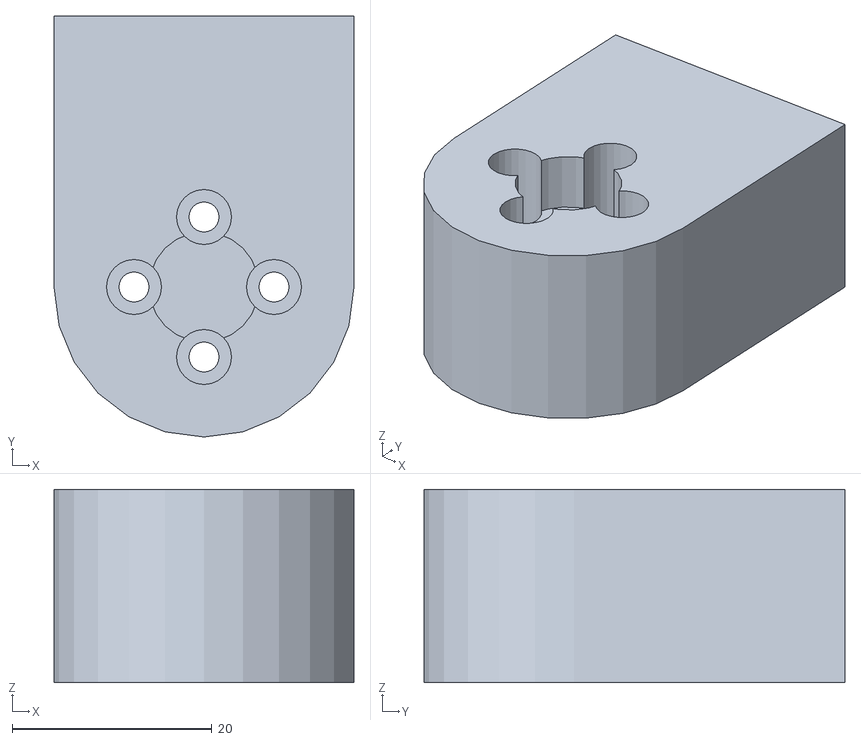
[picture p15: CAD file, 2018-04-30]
Mechanical/right_pivot.stl
30.0 x 42.1 x 19.4

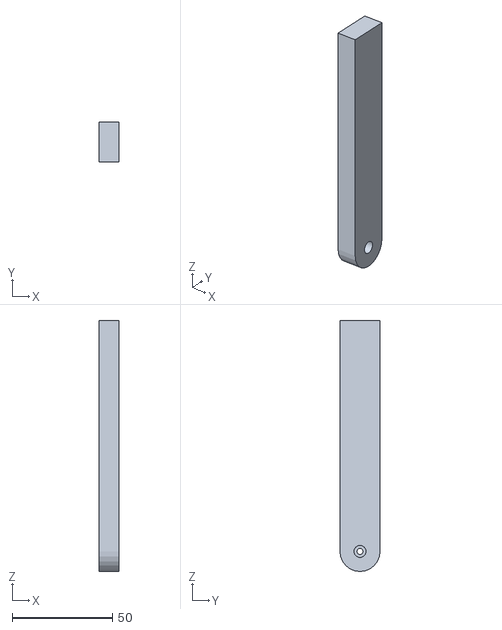
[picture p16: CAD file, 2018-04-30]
Mechanical/left_armature.stl
10.0 x 20.0 x 125.0

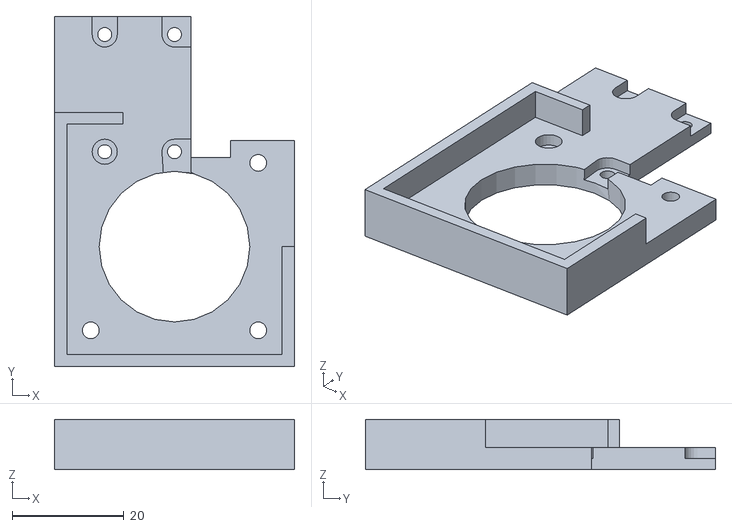
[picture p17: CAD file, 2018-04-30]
Mechanical/camera_mount.stl
43.0 x 62.7 x 9.00

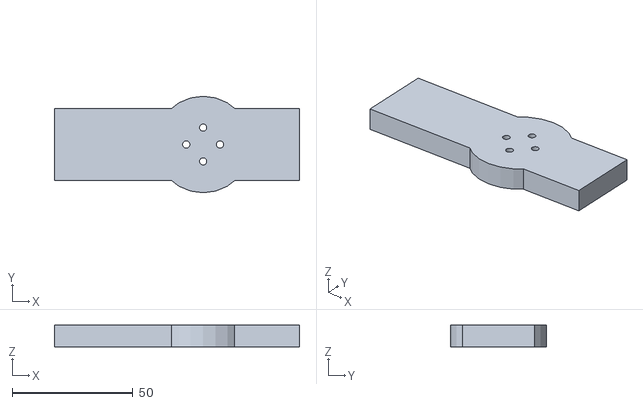
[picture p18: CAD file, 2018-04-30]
Mechanical/center_armature.stl
101.6 x 40.0 x 9.00

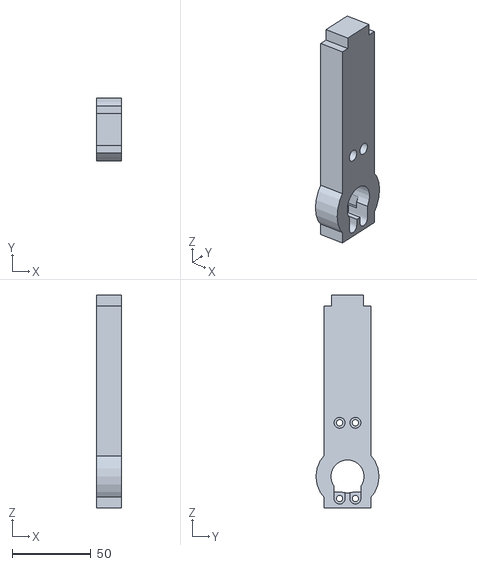
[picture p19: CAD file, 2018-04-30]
Mechanical/right_armature.stl
16.0 x 40.0 x 135.0

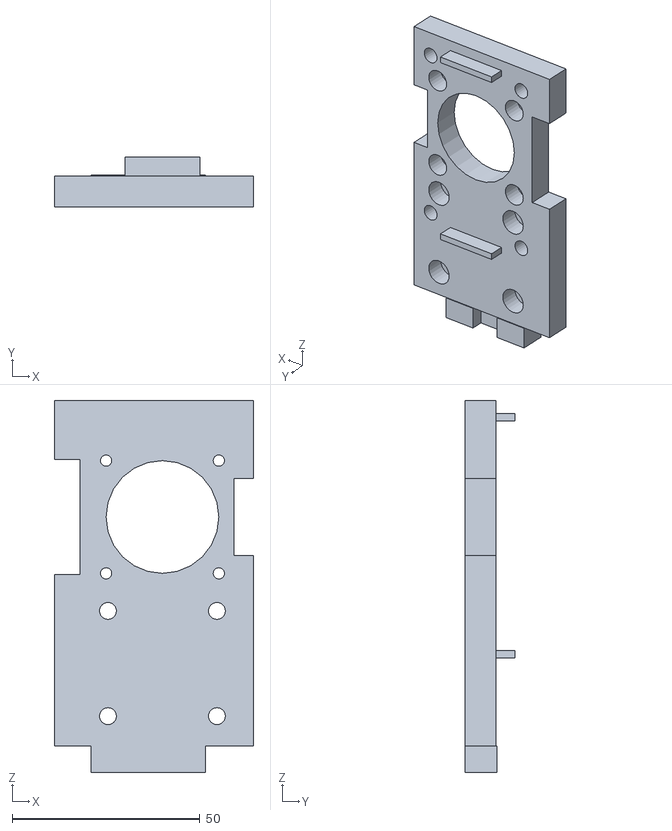
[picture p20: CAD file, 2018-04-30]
Mechanical/back_plate.stl
53.0 x 13.2 x 99.0

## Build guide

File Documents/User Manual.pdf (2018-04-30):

## Boston University Electrical & Computer Engineering

EC464 Capstone Senior Design Project

## User Manual

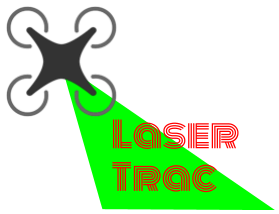
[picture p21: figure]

Submitted to:
Professor Thomas Little, PhD 8 St. Mary’s St., Boston
MA 02215, Room 426
(617) 353-9877
tdcl@bu.edu

by
Team #15 - LaserTrac
Aviva Englander | englanda@bu.edu
Christopher Liao | cliao25@bu.edu
Jeffrey Lin | jlin96@bu.edu
Anton Paquin | paquin@bu.edu
Eduardo Portet | eportet@bu.edu

Submitted: 04/18/2018

User Manual | 1

Table of Contents

Executive Summary | 2
Introduction | 3
System Overview and Installation | 4
Overview Block Diagram | 4
User Interface | 4
Physical Description | 5
Installation Setup and Support | 6
Operation of the Project | 7
Operating Mode 1: Manual Operation | 7
Operating Mode 2: Automatic Operation (not fully implemented) | 7
Operating Mode 3: Abnormal | 8
Technical Background | 9
Coarse Tracking Algorithm | 9
Fine Tracking | 9
Photodiode Array and Circuit Board Design | 9
RF Transceiver (nRF24L01) | 10
LIDAR | 10
Tracking Algorithm | 11
MEMS Mirror | 12
Particle Photon | 12
Cost Breakdown | 13
Appendices | 14
Appendix A: Technical Information | 14
Appendix B: Team Information | 18
Team 15 - Laser Tracking | 04/18/2018

Executive Summary

Laser Tracking and Communication with UAVs Team 15 - LaserTrac

As the radio spectrum becomes more crowded, interference has become an increasingly urgent problem. Wireless Optical Communication (WOC) has emerged as an attractive alternative to radio communication, since it can be aimed at a specific point. Currently WOC is used between stationary objects in many cities, where the transmitter is often mounted on top of skyscrapers to ensure clear line-of-sight. However, WOC with moving targets is still being researched.

The goal of our project is to maintain two-way WOC with an Unmanned Aerial Vehicle (UAV). In order to accomplish this goal, the problem of tracking a moving object must be solved. We intend to use the laser used for communication to track the UAV. While both WOC and laser tracking are well researched, there is little prior work focused on accomplishing both communication and tracking with one laser device. Potential applications for our project include providing internet access to disaster areas, drone racing, and air traffic control.

### 1. Introduction

Wireless optical communication has many benefits when compared with radio frequency communication. Currently the radio frequency spectrum is cluttered and requires a license for use. Our goal is to implement an alternative method for rapid data transmission, that doesn’t require a license. What differentiates optical communications from radio frequency communications is its high data rate capabilities and ultra dense access point deployment. Free space optical communications can potentially transmit data at rates of up to Gbps. This is why optical wireless communication is a viable alternative to radio frequency communications.

This method of communication has some characteristics which make it difficult to implement for practical purposes. The most pressing issue with using optical wireless communication is that in order for data to be transmitted, the laser must be pointed at a receiver. This means that the azimuth and elevation angles of the target with relation to the transmitter must be known to within an extremely high degree of accuracy. This is not an issue for communicating with stationary receivers. However if optical communication is to replace radio frequency, it must be able to transmit data to moving receivers. In the past, work has been done by another senior design group with two dimensional motion and knowledge of the receivers’ trajectories. The challenge with our project compared with the past work was that we were tracking in three dimensions and with no prior knowledge of our receiver trajectory. Our project’s goal is to maintain a constant communication link with aerial vehicles. Without our project this communication link cannot be maintained for moving aerial vehicles resulting in gaps in communication and lost data.

We were provided with a MEMS mirror for pointing the laser and some base code for changing the position of the mirror. From that we constructed a feedback loop which we used to automate the reflection of the laser to keep it pointed at our receiver which is attached to a rapidly moving unmanned aerial vehicle.

### 2. System Overview and Installation

### 2.1. Overview Block Diagram

The functionality of this project is straightforward; it tracks a device mounted to a drone using visible light. Our laser tracking system has five main components on its outermost layer, the MEMS mirror beaming the laser, the photodiode array, a camera, a LIDAR and a pair of radio frequency transceiver modules.

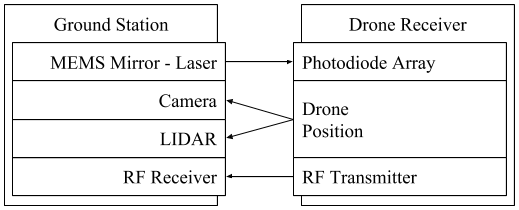
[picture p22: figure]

Figure 2.1: System Overview Diagram

The system works as follows, on startup the camera will locate the object and identify its position. Once identified it will address the laser and move it to point at the general direction of the target. Here the laser will scan the area until it makes contact with the photodiode array. The photodiode array will transmit the position of the laser as it hits the photodiodes, and the laser will then be able to readjust moving back to the center of the array with assistance from the LIDAR.

### 2.2. User Interface

For this project we have little input from the user, but we still allow for some measure of customization. The coarse tracking algorithm is where all of our user interface can be found due to the wide range of scenarios that the product can be used and how they would affect the traceability of the transmitter. To this end we enable the user to tweak the HSV range specifications for the most accurate tracking.

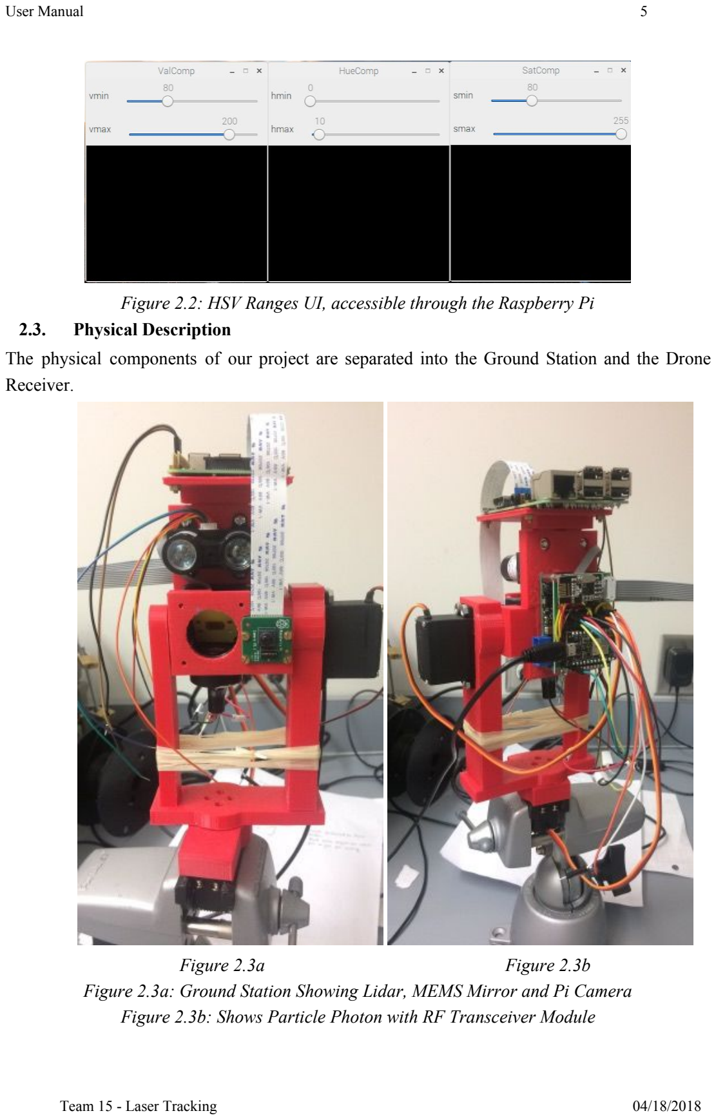
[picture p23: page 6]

Figure 2.2: HSV Ranges UI, accessible through the Raspberry Pi

### 2.3. Physical Description

The physical components of our project are separated into the Ground Station and the Drone Receiver.

Figure 2.3a | Figure 2.3b
Figure 2.3a: Ground Station Showing Lidar, MEMS Mirror and Pi Camera Figure 2.3b: Shows Particle Photon with RF Transceiver Module

The Ground Station is composed of a base that holds everything in place and ensures minimal movement of the parts. Mounted on the metal base is a 2-part 3D printed encasing. Each part of the case holds a Servo motor to enable pan and tilt movement. The tilting section of the case contains the Raspberry Pi, the Pi Camera Module, the LIDAR, the Photon and of course the MEMS mirror with the laser attached to it.

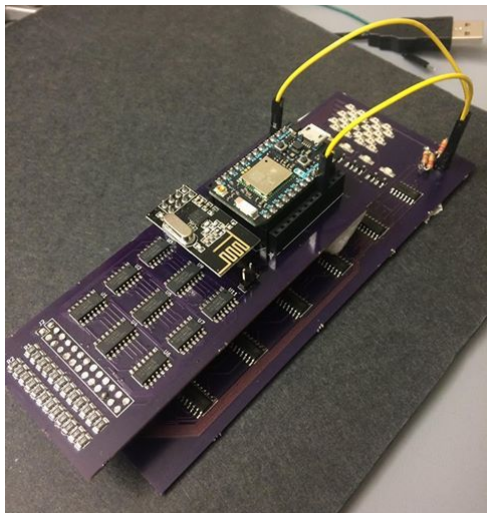
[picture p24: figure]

Figure 2.4: Drone Receiver PCB with Particle Photon and RF Transceiver

The Drone Receiver consists of two printed circuit boards, a particle photon and a RF transceiver. The sensor board and the mux board are designed to connect vertically via the 2x13 connector near the bottom edge of each board. This connector is designed so that it cannot be connected in the wrong orientation. The mux board connects to the particle photon via two 1x12 headers. The photon must be attached in the proper orientation, with its micro USB port towards the edge of the board. The nRF24L01 transceiver attaches to the 2x4 header on the mux board, with the body of the transceiver facing in towards the rest of the PCB.

### 2.4. Installation Setup and Support

Given that the microcontrollers are already setup and the required dependencies are installed, the only initialization steps are to power up the devices. The power supply for the ground station should be set to output 5 volts by pressing the output button and twisting the knob until the display reads 5.00 volts.

### 3. Operation of the Project

In either mode of operation, the receiver boards each require a 5-volt power source. This can be provided by a drone’s BEC circuit, or by the AA battery pack provided. The +5V line should be connected to the pin closest to the “J1” label, and the GND line should be connected to the remaining pin. The sensor board has a sensitivity that can be configured by the resistor bridge near the power port. To reduce sensitivity, the user may reduce the resistance across “R1”, or increase the resistance across “R2”. Doing the opposite will increase the sensitivity of the sensor. To achieve communication, connect serial Tx to the pin indicated on the transmitter. Connect ground to pin indicated. This pin modulates the laser. Connect Rx to D7 of the the photon on the receiver. Connect ground pin to photon on receiver. The communication can be treated as a UART connection.
There are two separate power supplies needed for the transmitter. All transmitter components are powered through the RasPi. The RasPi should be powered by a wall adapter or laptop USB connection. Use a short micro USB cable to connect the Raspi to the Photon, this serves as serial connection and power supply for Photon, laser, LIDAR, MEMS, and radio. The servos must be powered separately via the jack indicated. This must be a 5V 5A power supply. A smaller power supply will result in erratic servo behavior.

### 3.1. Operating Mode 1: Manual Operation

Manual operation is fine tracking without coarse tracking integrated and requires that a human manually instantiate the initial laser lock on the target. This works similar to automatic operation in that once the laser is pointed at the receiver on the drone, it stays on the drone using the radio frequency feedback. The biggest difference between manual and automatic operating mode is that the user must initially place the receiver on the drone in front of the laser before it begins moving. This is true anytime the laser loses the drone, the human in the loop must take care of coarse acquisition instead of the raspi camera.

### 3.2. Operating Mode 2: Automatic Operation (not fully implemented)

There are two main modes of automatic operation. First there is the coarse acquisition which is the mode when the laser is pointed at the drone. The other mode is fine tracking when the laser is pointed at the receiver and the ground station is getting feedback from the drone.
In the first mode of operation the servos controlled by the Raspberry Pi are rotating around until the raspi camera detects the drone. Once the drone is detected the laser is pointed at the drone and the drone sends feedback to the ground station telling it which photodiode has been hit and the product transitions into the second mode of operation.

In the second mode of operation, the camera is no longer trying to find the drone. Instead the laser is being moved to try to keep it centered in the photodiode array. In order for the laser to be kept in the array successfully, the radio transmitter on the drone should be sending feedback which the ground station uses to calculate where the laser should move. If there is a temporary obstruction which causes the laser to lose the drone, we transition back to the first operation mode.
These two modes currently work independently of each other. We are currently working on integrating both modes together.

### 3.3. Operating Mode 3: Abnormal

Abnormal Operation occurs when the laser loses track of the drone because it is out of range. The system will only operate normally when the drone is in range. When the drone is not in range the laser will move around rapidly and the camera on servos in will move around somewhat spastically until either power is disconnected or the drone comes back in range.

### 3.4. Safety Issues

The laser used by the laser tracking system is eye safe, although the manufacturer recommends that it not be purposefully pointed into someone’s eyes. In addition the effects of staring directly into a laser may be exacerbated by the use of a lense that magnifies the intensity of the laser. Avoid contact with water for outdoor use.

### 4. Technical Background

Laser tracking can be broken down into two major components, Fine Tracking and Coarse Tracking. We must be able to find the object we are looking to track with our Coarse Tracking Algorithm before adjusting ourselves to aim at center of our target.

### 4.1. Coarse Tracking Algorithm

The coarse tracking algorithm is run from the Raspberry Pi. This code required extra processing power provided by the Raspberry Pi due to the volume of image manipulation that was is required to track an object constantly. The Raspberry Pi Camera Module V2 was used to access the video stream, however any USB camera with a minimum quality of 720p can also be used.

This algorithm utilizes the library OpenCV for all of its camera related manipulations and video retrieval. The video resolution is set to 320x240 pixels for improved performance on the Raspberry Pi and reducing lag. Once the video stream is introduced to the algorithm it will enter a while loop that will first blur the image using a Gaussian blur to get rid of any sharp edges that will interfere with the image processing aspects. Once blurred, it will separate the image of that instance into 3 different spectrums; hue, saturation and value. Each instance will provide a different visibility range that can be overlapped to obtain a trace of the tracked object. Once we overlap these images we run two iterations of eroding and dilatation masks to discard any unwanted smaller blobs, as OpenCV refers to the overlapping figures. The program will then select the larger visible blob, find its center of mass and record this position as (x,y) where the position represents the pixel location. This process occurs for each frame of streamed footage and is extremely taxing on the Raspberry Pi.

In order to communicate with the Photon controlling the laser position and servos, we use serial communication through USB to transfer the recovered information from the previous steps.

### 4.2. Fine Tracking

Fine tracking has several key components, the array of sensors on the receiver and circuit board, the radio frequency transceiver, the lidar, the actual tracking algorithm, the MEMS mirror and the particle photon.

### 4.2.1. Photodiode Array and Circuit Board Design

The receiver circuit consists of two PCBs, a particle photon, and a transceiver module. The PCBs are the “sensor” board, and the “mux” board.

The primary component of the sensor board is a 6x4 photodiode array which detects the presence and position of a red laser. These photodiodes produce an analog signal, which is then cleaned by comparison with a resistor bridge. The binary on/off data from each photodiode is made available outside the board via a 13x2 header. If used alone, each pin of output requires a pull-up resistor on its output. The sensor board’s resistor bridge is configurable to allow the optical sensitivity of the detection circuit to be changed after the board has been built.

The mux board makes the 24 signals from the sensor board available to the particle photon. The primary components of this board are a 32-to-1 multiplexer, and a 24-input OR gate. The multiplexer allows the photon to read each photodiode one at a time, which is used for detecting the laser’s position. The OR gate allows the photon to detect if the laser is present, which we use to transmit data across the laser link.

### 4.2.2. RF Transceiver (nRF24L01)

From the photodiode array, we are able to extrapolate data telling us where the laser is hitting our drone. Ideally we would want to use a laser to establish a backlink from the target/drone to our ground station relaying the relevant information however that would require us to create another Laser Tracker that would end up being far too large and too heavy to be placed on a drone. Our team decided that for the sake of the project, using an RF Transceiver would suit our needs well.

The RF Transceiver uses the 2.4 GHz band to communicate between devices. The transmitter and the receiver modules must be on the same “pipe” in the band in order to communicate properly. These modules are connected to our Particle Photon Microcontrollers via SPI and has a data rate of either 250Kbps, 1Mbps or 2Mbps.

These modules have a overhead of about 2ms from getting the information from the photodiode array and sending it out, to receiving it on the ground station. This model of transceiver is also limited in its range of 100m. Because it operates in the 2.4 GHz band, there may be a lot of noise coming from other comRF mon signals operating in the same frequency such WiFi and Bluetooth.

### 4.2.3. LIDAR

We use the Lidar to find the range of the drone and use that combined with the azimuth and elevation angles to determine how much we should adjust the angles of the laser in order to move it closer to the center of the photodiode array. The use of the lidar allows us to adjust for the varying range of the drone as the angles will differ greatly when the drone is 1 meter versus when it is 10-15 meters away. When the drone is farther away we want to make smaller adjustments to the angles of the laser and when it is closer bigger changes. Adding the Lidar will improve the range of ranges at which fine tracking will work. The Lidar has two main components, one which outputs a pulse of light and one that receives the reflection. The Lidar uses the time it takes for the light to travel to the target and back as well as the speed of light to calculate the distance between the lidar and the object that the light reflects off of. The lidar transmits the range of the target to the photon using a pulse width modulated logic signal. The photon measures how long the signal is high and uses the conversion rate, 10 microseconds high corresponds to 1 centimeter of distance. The lidar needs to be hooked up to a 5 volt power supply and ground to work.

### 4.2.4. Tracking Algorithm

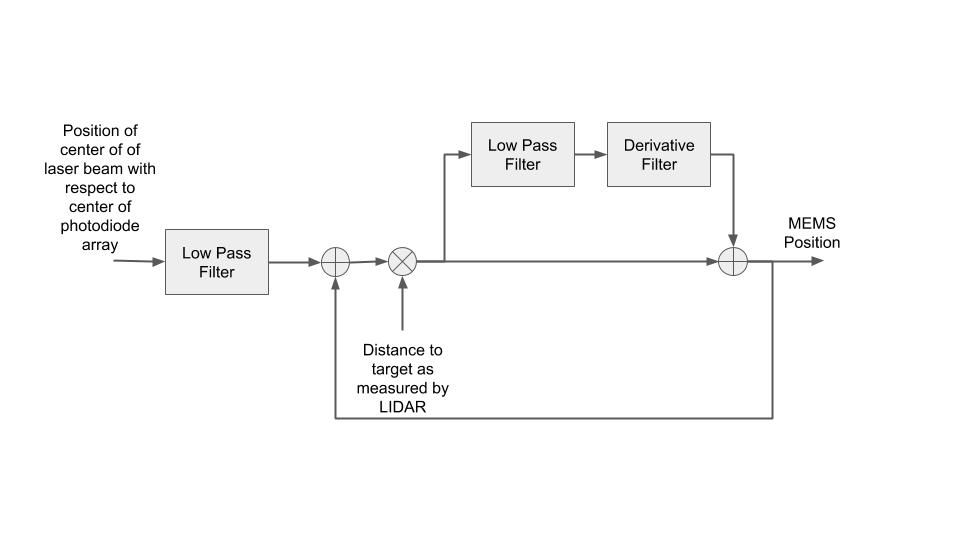
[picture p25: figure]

Figure 4.1 Tracking Algorithm Block Diagram

Simply stated, the tracking algorithm we use is a feedback loop where we move the laser in the direction of the center of the photodiode array. The simplest system would adjust the position of the MEMS by some constant times the distance from laser to target times the position from of the laser from the center of the array as measured by the photodiode array. In practice, tracking is complicated by (1) nonlinearity of voltage output to MEMS mirror with respect to distance distance moved by laser, (2) movement of servos, (3) latency of feedback signal, and (3) noise in the feedback signal.

We do not address the first issue (nonlinearity). We justify this by assuming that the MEMS does not move much from rest, so we can approximate a linear relationship between Δd and Δθ where

Δd is the distance between the center of laser beam and center of photodiode array, and Δθ is corresponding difference in angle the laser needs to move.

To address noise in the feedback signal, which is especially a problem with servo movement, we low pass filter the signal from the photodiode array. We average the past four values transmitted, but this filter is tunable. Averaging too many values causes delay in response from MEMS and poor tracking.

To address latency, we use a linear predictor to predict the next position of the photodiode array so that the tracking does not rely solely on feedback from the photodiodes. This linear predictor is implemented by a low pass filter and derivative filter as illustrated in Figure 4.1. The low pass filter is necessary, since the derivative filter is sensitive to noise. The derivative filter approximates the speed of the target over time using the last few positions. The result of the linear predictor is added to the adjustment needed to center the laser.

### 4.2.5. MEMS Mirror

The MEMS mirror is controlled by two voltages sent over SPI. The voltages control angle of the mirror around x and y axes. The maximal deflection of the mirror is 6 degrees in any of the 4 coordinate directions. Using our setup, the field of view of the MEMS is roughly a rectangle ± 12 degrees in y direction and ± 6 degrees in x direction. Calculating the relationship between the distance the laser point moves with respect to the target and the voltages applied to the MEMS is a relatively complicated geometric problem. We approximate a linear relationship, since the servo should do a good job keeping the MEMS centered.

### 4.2.6. Particle Photon

The Particle Photon is used to control both the receiver components and the transmitter components. The microcontroller used by Photon is part of the STM32F20 series microcontrollers. It is part of the Cortex M3 family. The Cortex-M3 programming manual and RM0033 Reference manual was consulted for this project. Major hardware functions needed include Timer counters and SPI. The TCs were programmed manually for the servos, as the Photon library has some issues with controlling two servos on two channels of same TC. TC needs to operated in capture mode for LIDAR and waveform mode for servos.

### 5. Cost Breakdown

The following parts list has been formulated to create a beta version of this project. The list makes sure to include the items that would make the product the most efficient and functional. The drone is not included on this list as it is not considered part of our product, the user would need to have one or something else to mount the receiver.

Projected Costs for Production of Beta Version

Item 1 | Quantity 1 | Description Laser Diodes (Pack of 10) | Unit Cost $2.59 | Extended Cost $2.59
2 | 1 | Raspberry Pi 3 | $40.00 | $40.00
3 | 2 | Particle Photon * | $19.00 | $38.00
4 | 1 | Sensor PCB (Minimum order: 3) | $180.20 | $180.20
5 | 1 | Mux PCB (Minimum order: 3) | $75.09 | $75.09
6 | 1 | RF Transmitters/Receivers (Pack of 10) | $11.98 | $11.98
7 | 1 | Raspberry Pi Camera Module V2 | $22.99 | $22.99
8 | 1 | Stepper Motor Driver DRV8825 | $11.59 | $11.59
9 | 2 | Stepper Motor NEMA 17 | $11.99 | $23.98
10 | 1 | 4 Quadrant Actuator MEMS A1M16.5 Micromirror * | $499.00 | $499.00
11 | 1 | LIDAR-Lite V3* | $129.99 | $129.99
12 | 1 | 3D Printed Encasing | $15.00 | $15.00
Beta-Version Total Cost | $1050.41
*Provided by customer

### 6. Appendices

6.1. Appendix A: Technical Information
Appendix 1: Engineering Requirements
Requirement Optical beam type | Value, range, tolerance, units Class 1 or Class 1M
Weight of receiver on drone | ≤ 100 grams
Battery powering receiver on drone | ~ 10mW
Coarse position of drone acquired | 5 seconds
Fine position of drone acquired | 1 second
Range of operation | 1 - 20 meters
Tracking speed | 10 m/s or 36 km/h
Data rate to receiver | ≥ 250 Kb/s

Appendix 2: Tracking Algorithm Block Diagram

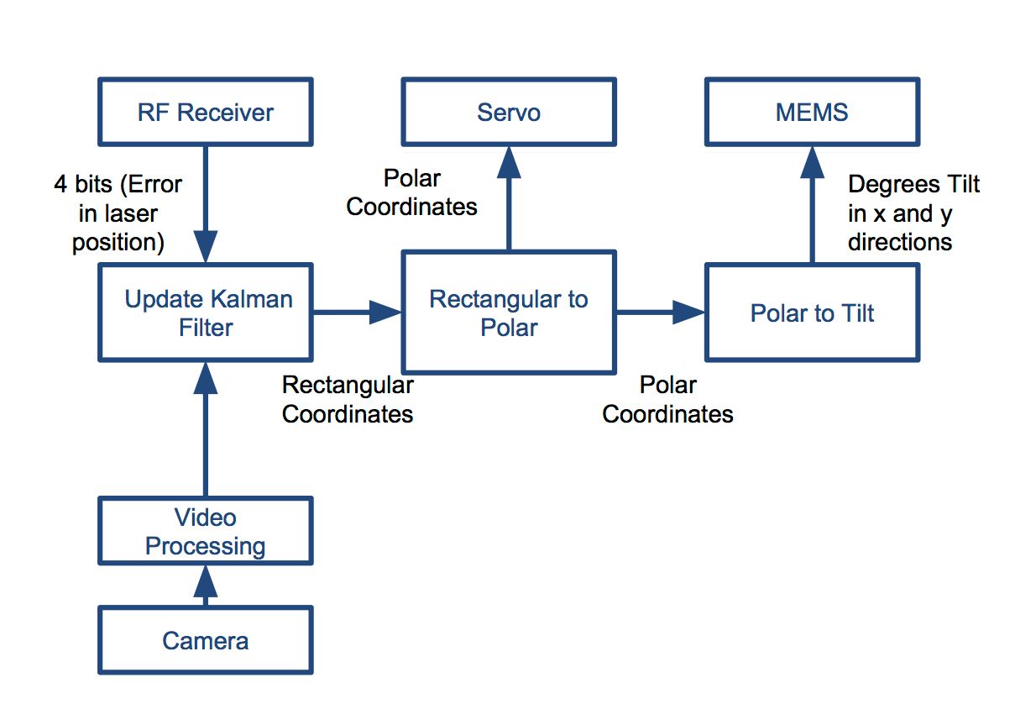
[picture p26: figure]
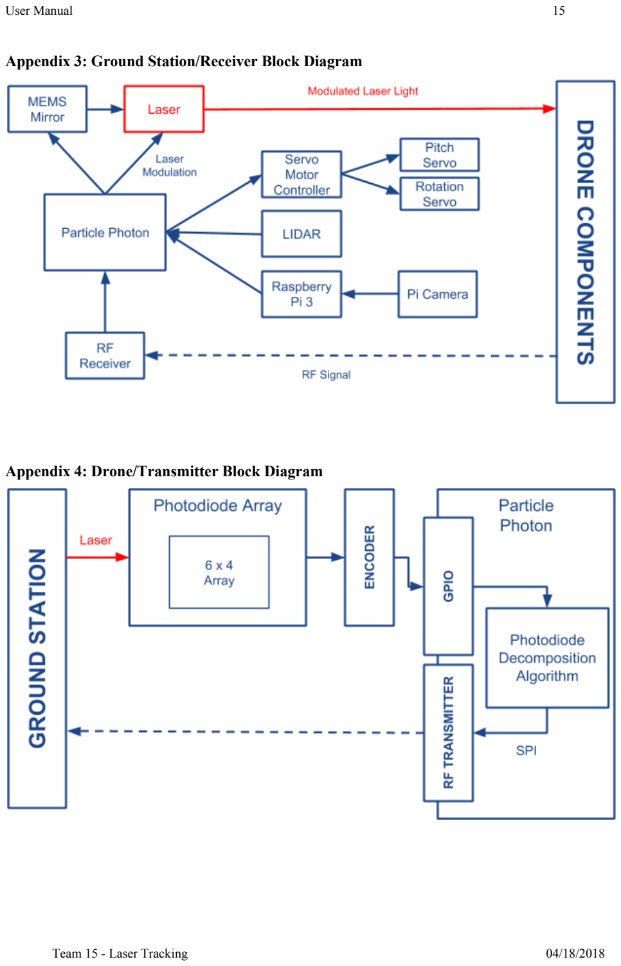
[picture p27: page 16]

Appendix 3: Ground Station/Receiver Block Diagram

Appendix 4: Drone/Transmitter Block Diagram

Appendix 5: Photodiode Circuit

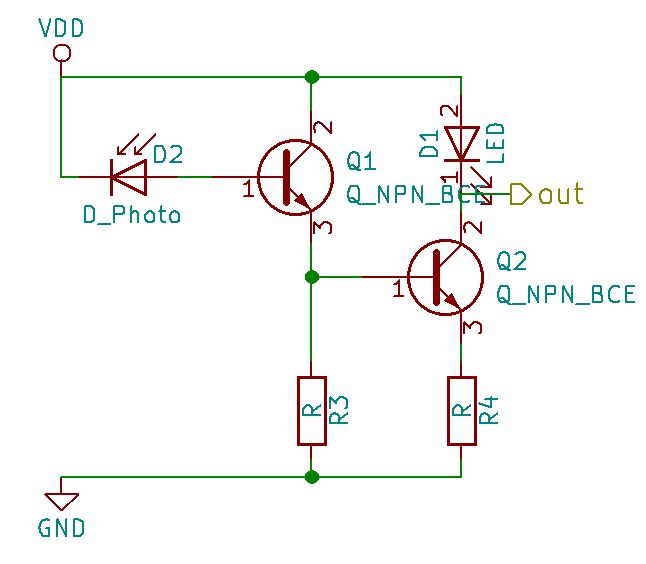
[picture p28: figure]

Appendix 6: Photodiode Array Design

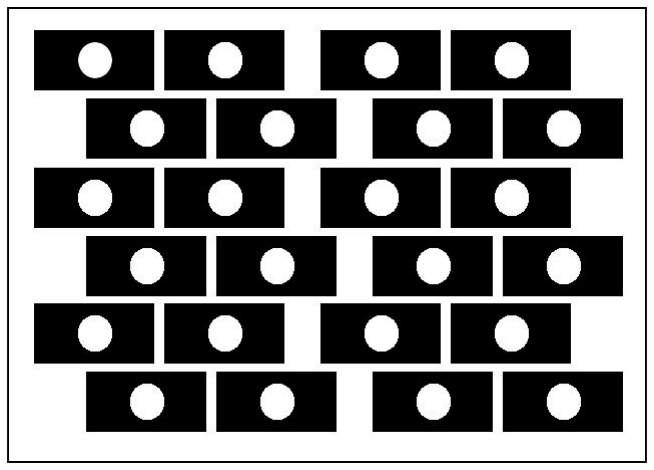
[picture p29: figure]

Appendix 7: PCB 3D Renders

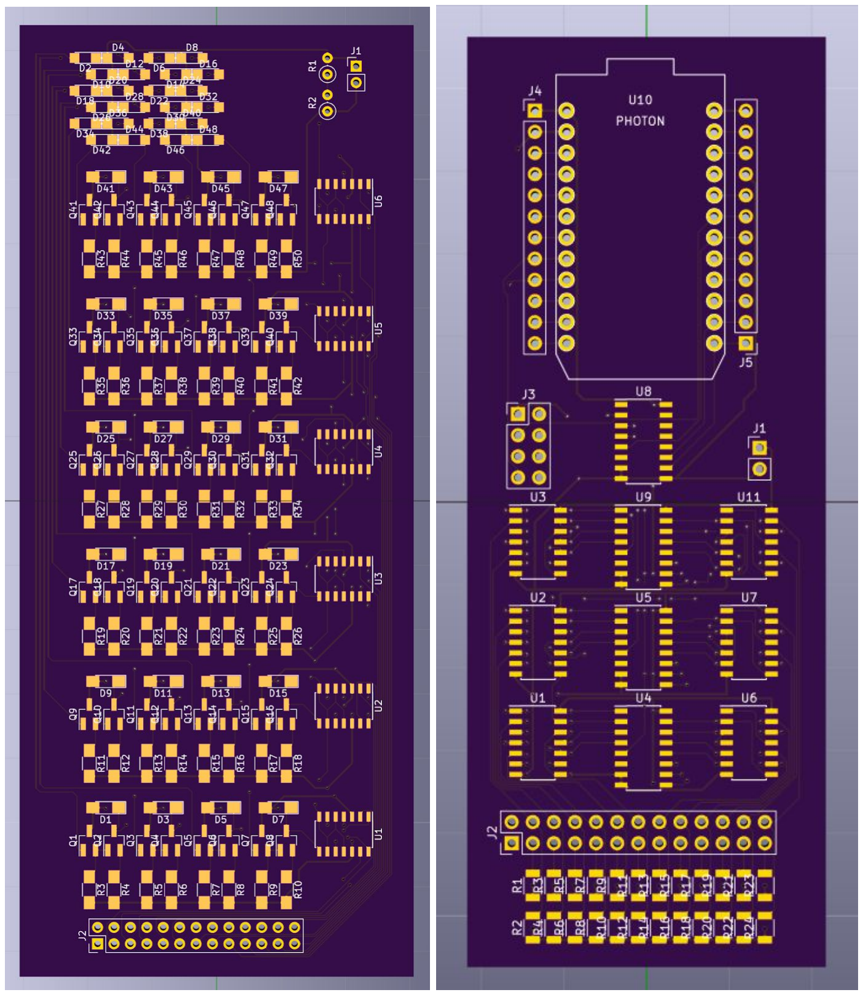
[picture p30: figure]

6.2. Appendix B: Team Information

Aviva Englander englanda@bu.edu
Aviva is a senior in Electrical Engineering. She is responsible for integrating the Lidar into the rest of the fine tracking mechanism. Her interests and experience lie primarily in signal processing and probabilistic graphical models.

Christopher Liao cliao25@bu.edu
Christopher is a senior studying Computer Engineering. Christopher developed the fine tracking algorithm and worked on the software that controls the MEMS mirror and designed and 3-D printed the casing which was necessary to integrate all components of the ground station.

Jeffrey Lin jlin96@bu.edu
Jeffrey is a senior studying Computer Engineering. He is responsible for the RF communication in the backlink to ensure the project has a closed loop. He is interested in software development where his experience in development is primarily in C/C++ and Python.

Anton Paquin paquin@bu.edu
Anton is a senior in Electrical Engineering. He designed the Photodiode Array and the PCBs essential in the project.

Eduardo Portet eportet@bu.edu
Eduardo is a senior in Computer Engineering at Boston University. He designed the coarse tracking algorithm and communication protocols between the Photon and the Raspberry Pi. He is interested in software developing and has development experience with Python, C/C++, C#, Java, Go and Ruby.

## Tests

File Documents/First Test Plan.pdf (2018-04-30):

# Memo

To: | Professor Pisano, Professor Alshaykh, Professor Hirsch
From: | Christopher Liao, Anton Paquin, Jeffrey Lin, Eduardo Portet, Aviva Englander
Team: | 15
Date: | 11/16/17

Subject: Preliminary Testing

### 1.0 Arduino to Arduino Optical Communication

1.1 Description of Test
We will demonstrate the optical communication aspect of our project by programming an Arduino Leonardo to “talk to itself” using laser communication. The Arduino Leonardo has two serial channels: Serial to communicate with the computer and another connected to pins 0 and 1 of the board (Serial1). This simple program listens for a message on Serial, then sends that message on pin 1 (Tx of Serial1). Serial1 Tx is connected to a laser, which is aimed at the photodiode in the receptor circuit. The receptor circuit’s output is connected to Rx of Serial1. When Serial1 hears a message, it is transmitted to the computer’s serial console via Serial.

When the circuit is setup and program is loaded, any message sent to the Leonardo should be echoed back to the computer’s Serial console. The tester will type the message “Hello World!” into the computer’s serial console and verify that it is echoed back to the console. The tester should increase the baud rate on Serial1 (the laser serial port) and re-perform the test until the message echoed back is corrupted.

1.2 Significance of Test The object of this test is to test the communication aspect of our project. Since the purpose of the project is to maintain laser communication with a moving target, establishing laser communication is an integral part. A successful test will have demonstrated that the receptor circuit and laser modulation mechanism work. Going from one Arduino talking to itself to one Arduino talking to another Arduino is trivial, since it does not involve any hardware or software changes.

1

Moving forward, two main tasks need to be accomplished to transition from this test to the communication mechanism need for the final product:
1. Rehauling hardware to allow for higher bitrate.
2. Making sure communication distance satisfies our design requirements.

1.3 Equipment and Setup
This test will require a computer, an Arduino Leonardo, and circuit connected according to the figure below:

1.4 Data Collection
The data received by and transmitted by the arduino.

1.5 Measurable Criteria
We will be measuring whether the data we transmit is the same as the data received by the photodiodes.

### 2.0 Tracking

2.1 Description of Test
In this test we will demonstrate a rudimentary laser tracking mechanism. This test will use a laser (always on) mounted on a stepper motor and two photodiodes as the receiver. As the receptor moves left and right, the stepper motor should be able to follow it.

The stepper motor is programmed to turn at a constant speed. When the laser hits the left photodiode, an interrupt is triggered and the motor changes its direction to move right. When the laser hits the right photodiode, an interrupt is triggered and the motor turns left. Thus, then the receptor assembly is held still, the laser should bounce back and forth between the two photodiodes. When the receptor is moved laterally, the laser should follow it as long as the beam is kept between the two photodiodes. If the receptor is moved too quickly and the beam is no longer between the two photodiodes, the tracking mechanism fails.

2

2.2 Significance of Test
Tracking is the second of our two main problems in this project, and also the more difficult. While the tracking setup demonstrated during this test is primitive, it is a good base to build more sophisticated tracking mechanisms upon. This test demonstrates our ability to control the laser with a servo and to maintain a feedback loop between the receiver and transmitter using photodiodes.

2.3 Equipment and Setup
Two photodiodes taped together connected to a circuit that sends feedback to an Arduino. Stepper Motor that is currently connected to the same Arduino. Laser glued onto Stepper Motor currently powered by a constant on source from the Raspberry Pi.

2.4 Data Collection
The data would be to verify that a stepper motor changes direction when the appropriate photodiode is hit.

2.5 Measurable Criteria
The metrics we will use for this test are the ability of the laser to follow the receiver which we will move a few cm to the left and right as well as the greatest distance from the laser where tracking will work.

3

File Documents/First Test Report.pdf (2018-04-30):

To: | Professor Pisano, Professor Alshaykh, Professor Hirsch
From: | Christopher Liao, Anton Paquin, Jeffrey Lin, Eduardo Portet, Aviva Englander
Team: | 15 - Laser Trac
Date: | 11/19/17

Subject: First Deliverable Test Report

### 1. Project Objective

1.1. The overall objective of our project is to create a optical based tracking and communication system from a ground station to a UAV, allowing users to interact with their vehicles without using Radio Frequency communication.

### 2. Test Objective and Significance

2.1. Our first two tests were significant because they demonstrated our ability to complete two fundamental areas of our project. First and foremost we demonstrated our ability to use optical wireless communication. The objective of this test was to prove that we could send bits using a laser and receive and read them using receiver. This is important because until we have working optical wireless communication, tracking the drone with a laser is a useless exercise. Once we achieve this first objective, we can focus on the more difficult problem at hand, our tracking mechanism.
2.2. Our second test focused on achieving a rough example of a tracking mechanism. With this test we demonstrated an ability to track an object with a laser while utilizing a photodiode array in the way we hope to for our final project. We started out with tracking an object moving left to right, which only required shifting the azimuthal angle of the rotating laser. This is a significant first step in the tracking problem. The most important part of this test is how we incorporated the photodiode array into the tracking process. This is a technique we hope to use in our final solution to the laser tracking problem.

### 3. Equipment and Setup

3.1. Receiver Circuit


Figure 1. This is the circuit diagram of the photodiode circuit. The output is a digital value. The leds on the right act as indicators. When the photodiode sees light, the output is HIGH, otherwise it is LOW. 5V power provided by wall adapter.

3.2. Laser Control Circuit

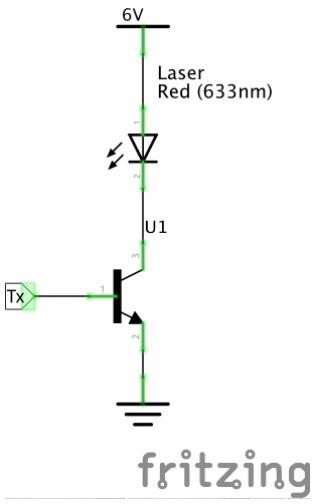
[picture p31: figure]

Figure 2. The laser is switched on and off by the Tx port using an NPN transistor. This circuit can be directly connected to the Tx wire of a serial port. 6V provided by 4 AAA batteries.

3.3. Stepper Motor Circuit
The stepper motor is not what we will use in the final product, but it is used for this preliminary test. The stepper motor we use is a cheap unipolar motor 28BYJ. The motor has 64 steps per revolution and is geared 64:1. This means that in half-step mode (which we use), there are 4096 steps per revolution.

The ideal controller program would use timer interrupts to “step” the motor, so that the Arduino is free to do other calculations while driving the motor. However, for this test, we use delay instructions in the code to delay the appropriate amount between steps. The delay amount we set for this test is 5 milliseconds. This means that during the tracking test, the motor rotates at approximately 2.9 rpm. To change the direction of a stepper motor, simply go through the step sequence in reverse.

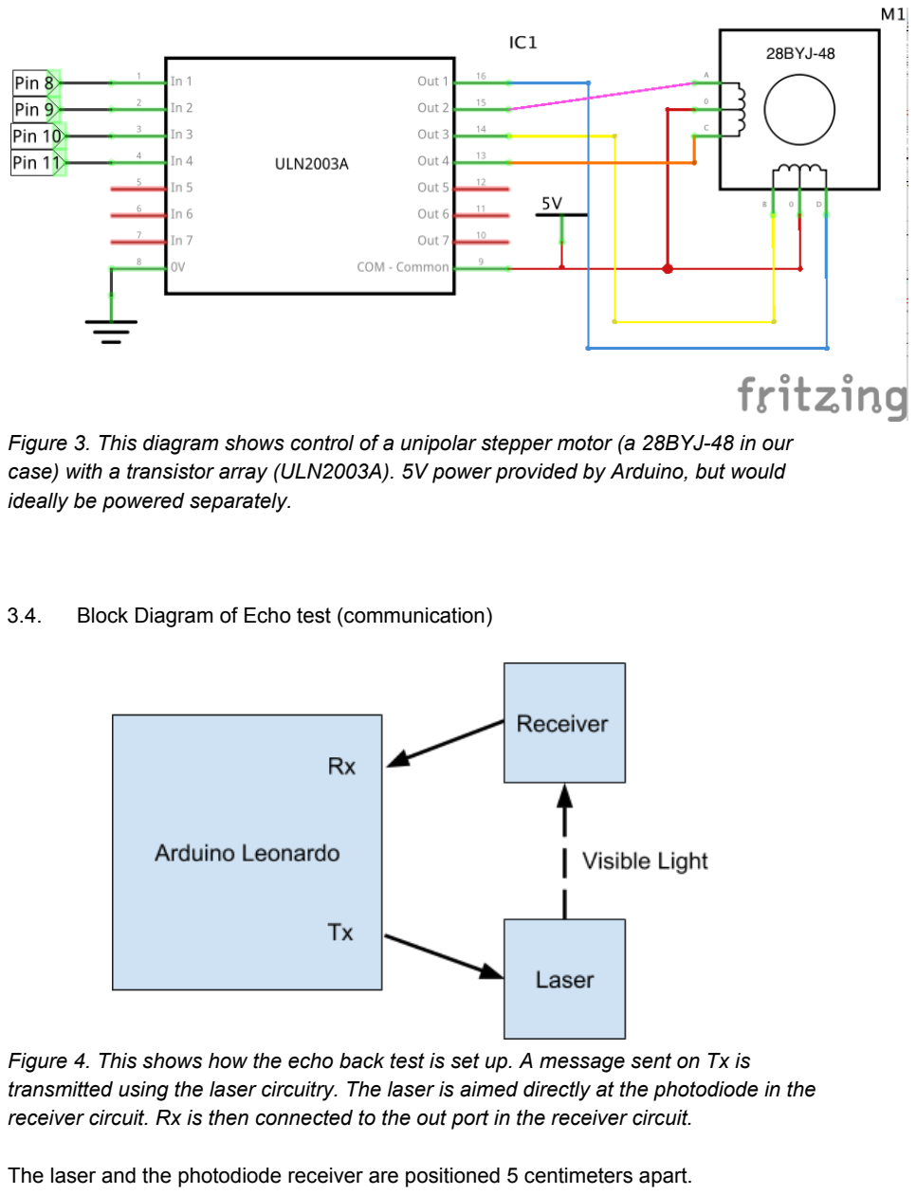
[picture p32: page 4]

Figure 3. This diagram shows control of a unipolar stepper motor (a 28BYJ-48 in our case) with a transistor array (ULN2003A). 5V power provided by Arduino, but would ideally be powered separately.

3.4. Block Diagram of Echo test (communication)

Figure 4. This shows how the echo back test is set up. A message sent on Tx is transmitted using the laser circuitry. The laser is aimed directly at the photodiode in the receiver circuit. Rx is then connected to the out port in the receiver circuit.

The laser and the photodiode receiver are positioned 5 centimeters apart.

3.5. Block Diagram of Tracking test

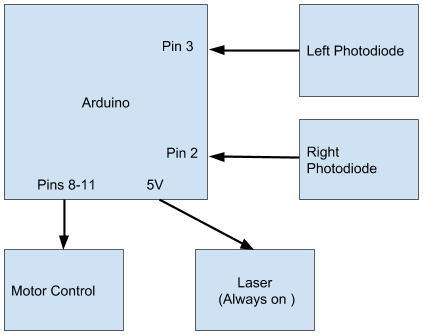
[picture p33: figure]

Figure 5. This shows how the Tracking test is setup. The Arduino controls the motor and receives input from the photodiodes. Pin 3 and 2 are set up as interrupt pins which trigger on the rising edge (when the photodiode sees light). The laser is always on. When the laser hits the left photodiode, the Arduino tells the motor to move right, and vice versa.

### 4. Measurements

4.1. Echo back Test

Testing the echo back, we sent the ascii character ‘U’(01010101) 1000x at varying baud rates, seeing at which baud rate would the communication start breaking down. We started at 9600 because it is a common communication rate. We found that communication falters at around 22000 baud. See appendix for more test baud rates.

Table 1. Percent of data corrupted compared to Baud rate of laser link. Laser and photodiode are 5 cm apart.
Baud Rate | Bytes Transferred | Bytes Corrupted | % Corrupted
9600 | 1000 | 0 | 0%
20000 | 1000 | 0 | 0%

21875 | 1000 | 0 | 0%
22000 | 1000 | 1000 | 100%
25000 | 1000 | 1000 | 100%
4.2. Tracking Test

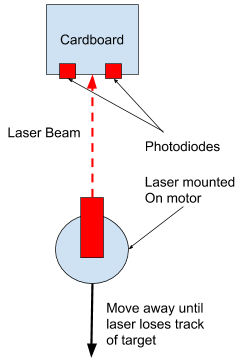
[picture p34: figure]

For this test, the distance between the two photodiodes is 4 mm. According to the procedure, we start with the laser directly in front of the photodiodes and 1 cm away. We then move the laser and motor away from the receiver without moving laterally as shown in Figure 6. We record the maximum distance between the laser and receiver assembly where the laser loses track of the receiver.

The laser loses track of the receiver at a distance of ~20 cm.

With the equipment that we have, we could not devise other controlled tests to test the tracking ability. The reason for this is 1) no reliable way of measuring speed, 2) lack of equipment (such as a rail) to ensure that the laser and receiver remain on the same horizontal plane, and 3) breadboard and wires are cumbersome.

### 5. Conclusion

5.1. In our first test we successfully passed bits from an Arduino to itself. In future tests we will be passing bits from our ground station to the drone. This test shows that we have viable methods for optical wireless communication. In future tests we will have to mount the photodiode array on the drone, and improve our tracking solution. However having the optical wireless communications working is a fundamental part of our project which we have successfully implemented.
5.2. From the second test we take note that although we have successful tracking results in the azimuthal direction, we still have many areas of our tracking mechanism that require development. In future tests we will add onto the photodiode array techniques that we have developed in our second test. Some areas for future development include tracking in the elevation and azimuthal direction together and improving the tracking algorithms that tell the laser how much to shift when it hits an outer photodiode in the array.

### 6. Appendix

6.1. Echo test code

int b;

void setup() {

pinMode(0,INPUT_PULLUP);
pinMode(1,OUTPUT);
Serial1.begin(10000); //Increase until failure }

void loop() {
if (Serial1.available()) { Serial.write(Serial1.read()); }
if (Serial.available()) {
Serial1.write(Serial.read()); }
}
6.2. Echo Test Full Table
Baud Rate | # Bytes Transmitted | # Bytes Received | # Bytes Corrupted | % Corrupted/ Not Received
9600 | 1000 | 1000 | 0 | 0
20000 | 1000 | 1000 | 0 | 0
21000 | 1000 | 1000 | 0 | 0
21500 | 1000 | 1000 | 0 | 0
21750 | 1000 | 1000 | 0 | 0
21875 | 1000 | 1000 | 0 | 0
22000 | 1000 | 1000 | 1000 | 100
25000 | 1000 | 1000 | 1000 | 100
30000 | 1000 | 1000 | 1000 | 100
40000 | 1000 | 1000 | 1000 | 100

6.3. Tracking test code

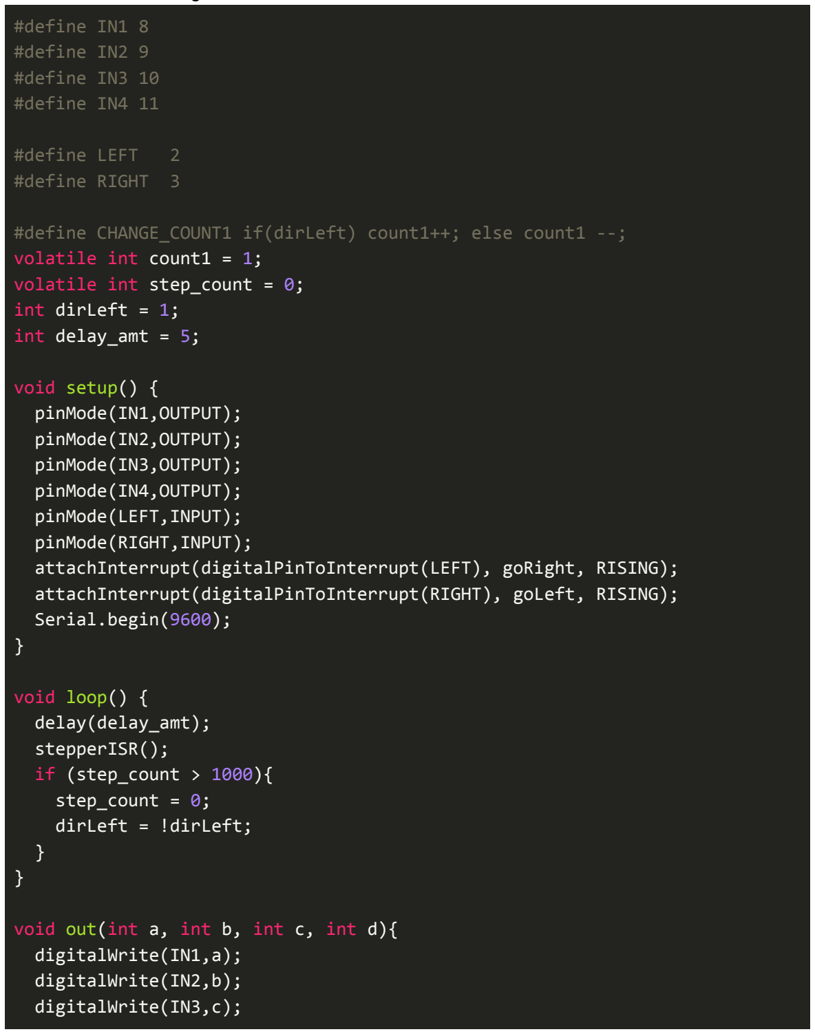
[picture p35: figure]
#define IN1 8 #define IN2 9 #define IN3 10 #define IN4 11; #define LEFT; #define RIGHT 3; volatile int count1 = 1; volatile int step_count = 0; int dirLeft = 1; int delay_amt = 5;; void setup() { pinMode(IN1,OUTPUT); pinMode(IN2,OUTPUT); pinMode(IN3,OUTPUT); pinMode(IN4,OUTPUT); pinMode(LEFT,INPUT); pinMode(RIGHT,INPUT);; Serial.begin(9600);; void loop() { delay(delay_amt); stepperISR(); if (step_count > 1000){ step_count = 0; dirLeft = !dirLeft;; void out(int a, int b, int c, int d){ digitalWrite(IN1,a); digitalWrite(IN2,b); digitalWrite(IN3,c);

#define CHANGE_COUNT1 if(dirLeft) count1++; else count1 --;

attachInterrupt(digitalPinToInterrupt(LEFT), goRight, RISING); attachInterrupt(digitalPinToInterrupt(RIGHT), goLeft, RISING);

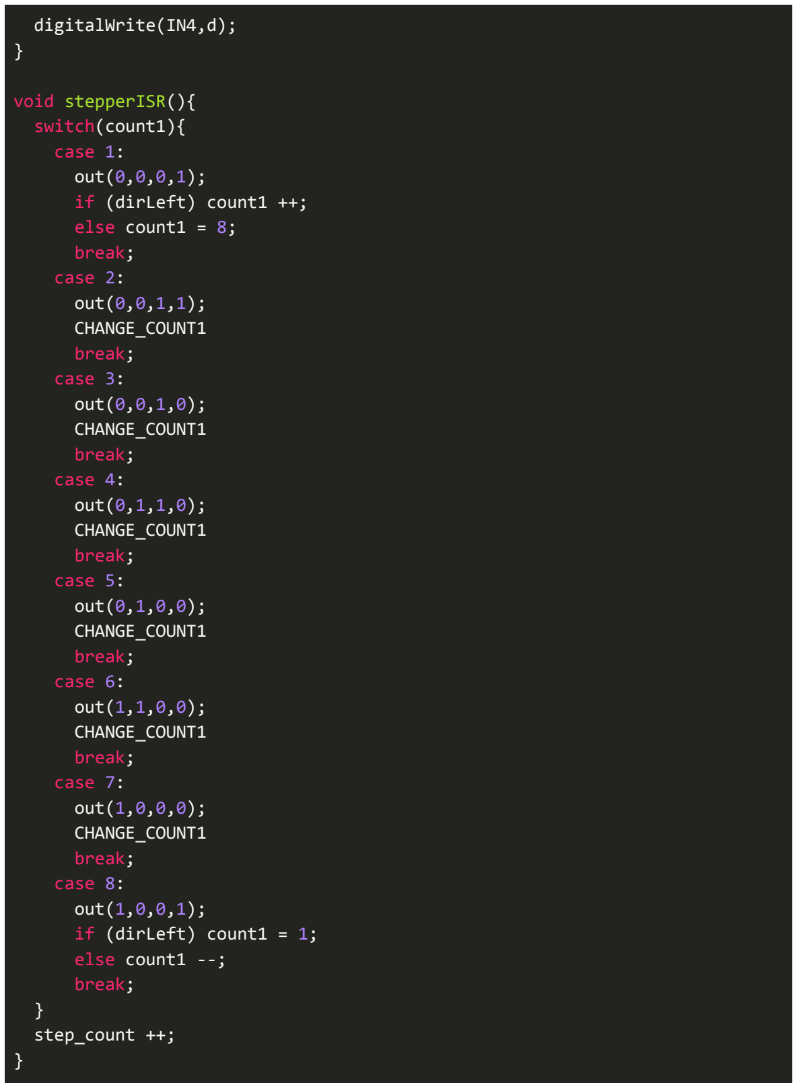
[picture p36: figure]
digitalWrite(IN4,d);; void stepperISR(){ switch(count1){ case 1: out(0,0,0,1); if (dirLeft) count1 ++; else count1 = 8; break; case 2: out(0,0,1,1); CHANGE_COUNT1 break; case 3: out(0,0,1,0); CHANGE_COUNT1 break; case 4: out(0,1,1,0); CHANGE_COUNT1 break; case 5: out(0,1,0,0); CHANGE_COUNT1 break; case 6: out(1,1,0,0); CHANGE_COUNT1 break; case 7: out(1,0,0,0); CHANGE_COUNT1 break; case 8: out(1,0,0,1); if (dirLeft) count1 = 1; else count1 --; break;; } step_count ++;

void goLeft(){
dirLeft = 1;
step_count = 0;
}

void goRight(){
dirLeft = 0;
step_count = 0;
}

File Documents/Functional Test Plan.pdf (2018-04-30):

# Memo

To: | Professor Pisano, Professor Alshaykh, Professor Hirsch
From: | Christopher Liao, Anton Paquin, Jeffrey Lin, Eduardo Portet, Aviva Englander
Team: | 15
Date: | 3/27/18

Subject: Functional Testing

### 1.0 Fine Tracking (Using MEMS)

1.1 Description of Test

In this test we will demonstrate a more sophisticated laser tracking mechanism. This test will use a laser (always on) being pointed with a MEMS mirror and a cluster of 24 photodiodes . As the target of 24 photodiodes moves (in any direction), the laser should follow the target.

The test will be conducted as follows: A person will hold the target (powered by 4 AA batteries) with 24 photodiodes and move around to demonstrate that the laser tracks the target, with the following restrictions:
- The target is always facing the laser. The angle of incidence measured with respect to the vector normal to the plane of the photodiodes should not exceed 30 degrees.
- The magnitude of the acceleration vector never exceeds ½*g.
- The magnitude of the velocity vector is unrestricted.
- The target is over the horizontal plane.
- Line of sight is maintained between the laser and the target.
- Ambient light is not excessive. (Testing in SLURP is possible during anytime of day with lights on and shades closed, but testing in Senior Design lab is impossible during daylight hours).
- Distance between the target and the laser exceeds 2.5 meters. We have not found an upper limit on this distance. The target can be tracked anywhere inside SLURP when it is at least 2.5 meters away.

1.2 | Significance of Test
| As mentioned before, tracking is the main problem in this project. This tracking method is much more sophisticated than what was previously demonstrated and shows significant progress toward meeting requirements.
1.3 | Equipment and Setup
| The mechanical setup is as follows: MEMS mirror with an field of view +/- 6 degrees in either direction is mounted on servo mechanism with two degrees of freedom. The servos are able to aim the laser in any direction above the horizontal plane. The goal of the servo is to increase the field of view of the laser. The servo will try to keep the MEMS mirror position centered to prevent the target from moving outside of the field of view of the MEMS.
| The goal of the MEMS is to keep the laser centered on the target. The MEMS is necessary, since it is capable of more rapid and precise movement than the servos.
| The following diagram is a high level system diagram of our setup. (numbered arrows are explained on next page)

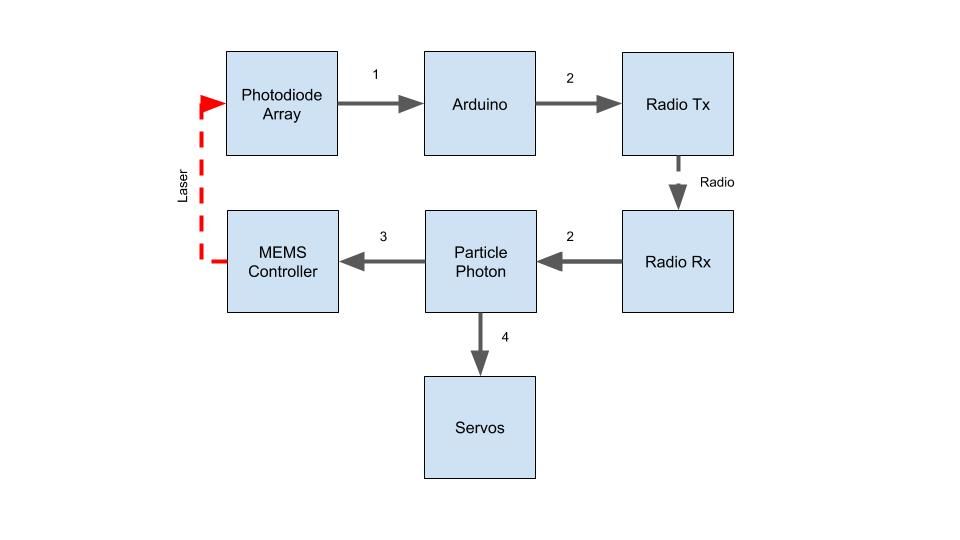
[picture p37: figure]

1. Photodiode communicates the digital state of each of the 24 photodiodes to the Arduino on the target. This is done by connecting the output of each photodiode to a multiplexer input. The Arduino shifts through all the diode ids (from 1 to 24) and reads the output.
2. The Arduino averages the coordinates of the diodes that are on to obtain the approximate coordinate of the center of the laser beam with respect to the center of the photodiode array. This coordinate (8 bits for x and 8 bits for y) is transmitted to the particle photon.
3. Using the error coordinates from the photodiode array, we generate the new pair of voltages to send to the MEMS controller.
4. Using the position of the MEMS as the error function for PID control, we generate a new pair of coordinates for the Servos to move to.
1.4 | Data Collection
| We are interested in the following data: ● Maximum acceleration at which we can move the photodiode array before the laser loses track of the target. ● Minimum distance between the MEMS and the photodiode array to achieve reliable tracking.
1.5 | Measurable Criteria
| The test is successful if the laser track the photodiode array given that the restrictions mentioned in section 1.1 are adhered to.

### 2.0 Coarse Tracking (Using Camera)

2.1 | Description of Test
| In this test we demonstrate our ability to track the coarse position of an object using the Raspberry Pi and a the Pi Camera. The test analyzes the input from the camera to isolate the desired object by looking at specific ranges of the hue, saturation and color value found in the image. The output of this operation would allow us to know the x,y position of the object tracked in terms of the image’s resolution (i.e. pixel height, pixel width).
| The Raspberry Pi will be able to control the servo movement to track the position of the object as it moves to prevent it from escaping the camera’s field of view. As we track the

object and get it’s relative position we can communicate with the Photon via USB Serial to transmit this information.

Once an object to track has been defined and its hue, saturation and value ranges have been defined.

The test will be conducted as follows:
The object tracked will be placed in the field of view of the camera. The image displayed will show a circle surrounding the object tracked and a red dot at the center of mass of the object. If the object moves outside of the central area of the camera’s view it will trigger the servos to maintain the object at the center.

The biggest limitations of this tracking mechanism is that it is very dependant on the lighting that the object is receiving. The HSV range need to be very flexible in order to track in most environments, but this will also cause the algorithm to get confused with other objects that might also fall within the same HSV range.

2.2 | Significance of Test
| In the overall outcome of the project the necessity for a coarse tracking mechanism exists in order to make the system as autonomous as possible. In this manner, the whole system would be able to function without needing human interference to initiate the contact between the laser and the photodiode array. The system would just rely on the coarse tracking algorithm to eventually find the tracked object, and relay its position to the MEMS mirror for fine tracking.
2.3 | Equipment and Setup
| The setup consists of a PiCamera V2 mounted on servo mechanism with two degrees of freedom. A Raspberry Pi connected to PiCamera V2 and to two servos. Pan servo mechanism connected to GPIO pin 12, and Tilt servo mechanism connected to GPIO pin
18. The Photon connected to a Raspberry Pi USB port used for communication between
| coarse and fine tracking.

2.4 | Data Collection
| The test will demonstrate data output for the object that is being successfully tracked and the servo movements that are applied. This includes a live feed of the video captured, display an enclosing circle of the object tracked, and display of the center of mass of the object.
| Optionally, we can also display the hue, saturation and value masks and ranges that are being used to create blobs and locate the object.
2.5 | Measurable Criteria
| The test is successful if we are able to track a predefined object and successfully follow it as it tries to escape the camera’s field of view. The Raspberry also needs to communicate information with the Photon via Serial USB and blink the onboard LED.

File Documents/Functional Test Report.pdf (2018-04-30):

To: | Professor Pisano, Professor Alshaykh, Professor Hirsch
From: | Christopher Liao, Anton Paquin, Jeffrey Lin, Eduardo Portet, Aviva Englander
Team: | 15 - Laser Tracking
Date: | 04/01/18

Subject: Functional Test Report

### 1. Project Objective

1.1. The overall objective of our project is to create an optical based tracking and communication system from a ground station to a UAV, allowing users to interact with their vehicles without using Radio Frequency communication.

### 2. Test Objective and Significance

2.1. This test was significant because it demonstrated our ability to track the sensor, which is a fundamental component of our project. Our core deliverable is a tracking algorithm, which we demonstrated. This test focused on achieving a fine tracking mechanism. With this test we demonstrated an ability to track an object with a laser once we had acquired it. We utilized our printed circuit photodiode array and radio frequency transmitter to do so. We successfully demonstrated a 3-dimensional tracking system which could follow the array at the expected speeds.
2.2. We have also demonstrated a rough coarse tracking algorithm that uses the Camera mounted on a Raspberry Pi. This tracking system will be integrated with the fine tracking before or during installation to assist in the initial localization of the photodiode array.

### 3. Equipment and Setup

### 3.1. PCB with Updated Photodiode Array

This is the main hardware component of of our project. The same circuit is used our current version of the PCB as the previous one.


This time, the photodiode circuit is tiled 24 times in our sensor array, arranged in the following pattern.

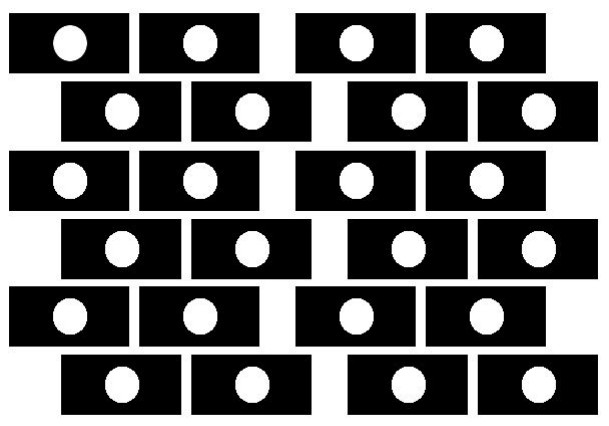
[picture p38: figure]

This design was created to minimize the likelihood of our laser passing in between the gaps of the photodiodes. Each output is treated as a single analog value, which is pulled low when the photodiode detects the presence of a laser.

### 3.2. Fine Tracking (Using MEMS Mirror)

For this test, the laser is steered by MEMS mirror, which is mounted on top of a servo mechanism. We use both MEMS mirror and servo mechanism since the MEMS is able to move quickly and precisely, but has a limited field-of-view (6 degrees in either direction). The servo is imprecise due to limitations of the potentiometer used for positioning and internal gears, but is able to extend the field-of-view of the MEMS to cover every point above the horizontal plane. The details of how this control is done is illustrated below.


Figure 4. This diagram illustrates the closed loop tracking system.

Description of signal path:

1. Photodiode communicates the digital state of each of the 24 photodiodes to the Arduino on the target. This is done by connecting the output of each photodiode to a multiplexer input. The Arduino shifts through all the diode ids (from 1 to 24) and reads the output.
2. The Arduino averages the coordinates of the diodes that are on to obtain the approximate coordinate of the center of the laser beam with respect to the center of the photodiode array. This coordinate (8 bits for x and 8 bits for y) is transmitted to the particle photon.
3. Using the error coordinates from the photodiode array, we generate the new pair of voltages to send to the MEMS controller. More precisely, let the error coordinates received be vector e. Then, the voltage output vector o can be expressed as,
o(t) = o(t - 1) + k * e(t) + (o(t) - o( t - i)) / i All vectors are pairs of x-y positions. Constant k can be tuned to change how the MEMS responds to error coordinates. Constant i, which we set to 100, adjusts how the velocity vector is calculated. Large i will make MEMS slow to respond to sudden changes in velocity, but low i will make it susceptible to randomness (noise) in the position of the laser.
4. This step was not demonstrated during functional testing. Using the position of the MEMS as the error function for PID control, we generate a new pair of coordinates for the Servos to move to.

### 3.3. Coarse Tracking Algorithm

In this test we demonstrated our ability to track the coarse position of an object using the Raspberry Pi and a the Pi Camera. The test analyzed the input from the camera to isolate the desired object by looking at specific ranges of the hue, saturation and color value found in the image. The output of this operation would allow us to know the x,y position of the object tracked in terms of the image’s resolution (i.e. pixel height, pixel width).

The Raspberry Pi will be able to control the servo movement to track the position of the object as it moves to prevent it from escaping the camera’s field of view. As we track the object and get it’s relative position we can communicate with the Photon via USB Serial to transmit this information, once an object to track has been defined and its hue, saturation and value ranges have been defined.

Once the object that we want to track enters the camera’s field of view, the image displayed will show a circle surrounding the object tracked and a red dot at the center of mass of the object. If the object moves outside of the central area of the camera’s view it will trigger the servos to maintain the object at the center.

The biggest limitations of this tracking mechanism is that it is very dependant on the lighting that the object is receiving. The HSV range need to be very flexible in order to track in most environments, but this will also cause the algorithm to get confused with other objects that might also fall within the same HSV range.

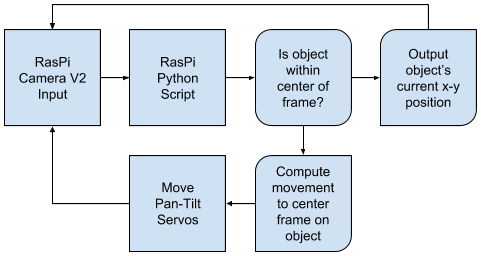
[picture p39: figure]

Figure 3. This diagram illustrates the control diagram that follows this algorithm.

### 4. Measurements

Due to the nature of our project, we are more concerned with building reliable hardware and software components to make closed loop tracking consistently, rather than taking concrete measurements. Here are some rough numerical measurements that are pertinent:

- Latency from shining light on photodiode to response from MEMS: 2 ms.
- Minimum distance across which tracking can be achieved: 2.5 meters.
- Maximum constant speed at which target can move with reliable tracking: 10 m/s.
- Maximum angle of incidence measured with respect to the vector normal to the plane of the photodiodes: 30 degrees.
- Maximum magnitude of the acceleration: ½*g.

All of the measurements taken above are rough estimates. We are unable to make precise measurements, since we lack the equipment to precisely measure quantities such as target acceleration and velocity.

### 5. Conclusion

5.1. In our test we successfully tracked an array of photodiodes. By the time of installation, we will be passing bits from our ground station to the drone. This test shows that we have viable methods for optical wireless communication. For installation, we will have to mount the photodiode array on the drone, and improve our tracking solution. However, having the optical wireless communications working is a fundamental part of our project which we have successfully implemented.
5.2. For the final test we implemented a coarse acquisition algorithm using a Raspberry Pi camera that was able to track an object and follow it using the servos on the mount.
5.3. Summary of next steps:

■ Integrate coarse and fine tracking so that they work together before or during installation
■ Send bits and track at the same time
■ Integrate Lidar to fine tune tracking by getting more exact angle for moving the laser
■ Integrate motion of servos with MEMS mirror in order to do fine tracking for wider range of angles

### 6. Appendix

Please note that for the Particle Photon Code, all tracking is done in the loop() function. The rest of the code declares various constants, variables, and support functions (most of which we did not write). The MEMS code is based on code provided by Emily Lam.

6.1. Fine Tracking Algorithm (Runs on Particle Photon)

void loop() {
// Set analog voltage X+, X-, Y+, Y- from center (analog_bias) always at 80 V
// Max voltage is 157 so max analog voltage is 157 - if you go beyond 157, the DAC will set to 80 V and your code won't work.

difX = 0; //Can be positive or negative
difY = 0;
incX = 0;
incY = 0;
setChannels(difX, difY);

while(1) {
while(! radio.available()); //wait for new communication radio.read(&radio_data, sizeof(radio_data[0])*2);
p++;
bufX[p] = difX;
bufY[p] = difY;
q = p+1;
if (p>=BUF_SIZE) p=0;
if (q>=BUF_SIZE) q=0;

incX = (bufX[p]-bufX[q])/BUF_SIZE; incY = (bufY[p]-bufY[q])/BUF_SIZE;
difX += incX;
difY += incY;
difX += (double)(radio_data[0])/127.0 * inc;
difY += (double)(radio_data[1])/127.0 * inc;

azimuth_servo_pos = azimuth_controller_update(difX); azimuth_write(azimuth_servo_pos);
setChannels(difX, difY);
serial_counter++;
if (serial_counter > 50){
Serial.print(difX);
Serial.print(',');
Serial.print(difY);
Serial.print(';');
Serial.println(azimuth_servo_pos); serial_counter = 0;
}
}
powerdown(); //Always power down at the end to disable the MEMS output.. If you don't do this and disconnect the power you may break the MEMS
}

int azimuth_controller_update(double mems_pos) { const double ki = 0.0, kp=0.1, kd=0.0; static double err_i = 0;
static double mems_last = 0;
double err_p, err_d;

err_i += mems_pos;

err_p = mems_pos;
err_d = mems_pos - mems_last;

mems_last = mems_pos;

return (int)(1500 + (err_i * ki) + (err_p * kp) + (err_d * kd)); }

void azimuth_write(int pos){
if (pos < 1200 or pos > 1800) return; azimuth_servo.writeMicroseconds(pos); }
6.2. Coarse Tracking Algorithm (Runs on Raspberry Pi)

def main():

usb = False | # True : Try to communicate with serial # False: Do not communicate
servo = True | # True : Communicate with the servos # False: Do not initiate servos
windows = 2 | # 0: Do not show any windows # 1: Show only the tracked window # 2: Show all the windows

# Set the (h,s,v) lower and upper bounds

lowerbound = (0,80,80)
upperbound = (10,255,200)

# Duty Cycle Values

# set to rest values

dc_p = 6.0
dc_t = 4.5

cap, port, pwm_p, pwm_t = setup(usb, servo, windows, lowerbound, upperbound)

while(1):

# MOVING SERVO

#pwm_p.ChangeDutyCycle(dc_p) pwm_t.ChangeDutyCycle(dc_t)

# Read frame

_, frame = cap.read()

# Blur the frame

blurred = cv2.GaussianBlur(frame, (5,5), 0)

# Converting to HSV

hsv = cv2.cvtColor(blurred, cv2.COLOR_BGR2HSV) hue,sat,val = cv2.split(hsv)

# Get info from track bar and appy to result if windows == 2:

lowerbound, upperbound = getBounds()

# construct a mask from the bounds obtained from trackbars, then perform # a series of dilations and erosions to remove any small

# blobs left in the mask

mask = cv2.inRange(hsv, lowerbound, upperbound)
mask = cv2.erode(mask, None, iterations=2)
closing = cv2.dilate(mask, None, iterations=2)

# find contours in the mask and initialize the current

# (x, y) center of the ball

cnts = cv2.findContours(mask.copy(), cv2.RETR_EXTERNAL, cv2.CHAIN_APPROX_SIMPLE)[-2] center = None

# only proceed if at least one contour was found

if len(cnts) > 0:
# find the largest contour in the mask, then use # it to compute the minimum enclosing circle and # centroid

c = max(cnts, key=cv2.contourArea)
((x, y), radius) = cv2.minEnclosingCircle(c)
M = cv2.moments(c)
if M["m00"] != 0:
center = (int(M["m10"] / M["m00"]), int(M["m01"] / M["m00"])) #dc_p, dc_t = moveServo(center[0],center[1], dc_p, dc_t) port.write(str(center)+"\n") if usb else None

# only proceed if the radius meets a minimum size

if radius > 10:
# draw the circle and centroid on the frame

cv2.circle(frame, (int(x), int(y)), int(radius),(0, 255, 255), 2) cv2.circle(frame, center, 5, (0, 0, 255), -1)

# display wanted windows

if windows == 1 or windows == 2:

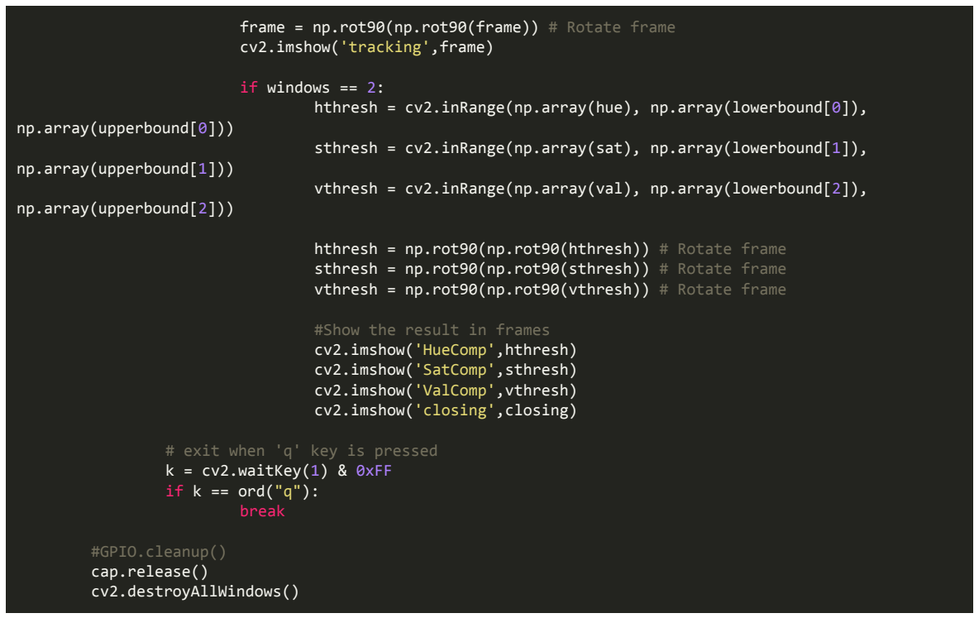
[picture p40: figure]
cv2.imshow('tracking',frame); if windows == 2:; np.array(upperbound[0])); np.array(upperbound[1])); np.array(upperbound[2])); #Show the result in frames cv2.imshow('HueComp',hthresh) cv2.imshow('SatComp',sthresh) cv2.imshow('ValComp',vthresh) cv2.imshow('closing',closing); # exit when 'q' key is pressed k = cv2.waitKey(1) & 0xFF if k == ord("q"): break; #GPIO.cleanup() cap.release() cv2.destroyAllWindows()

frame = np.rot90(np.rot90(frame)) # Rotate frame

hthresh = cv2.inRange(np.array(hue), np.array(lowerbound[0]),

sthresh = cv2.inRange(np.array(sat), np.array(lowerbound[1]),

vthresh = cv2.inRange(np.array(val), np.array(lowerbound[2]),

hthresh = np.rot90(np.rot90(hthresh)) # Rotate frame
sthresh = np.rot90(np.rot90(sthresh)) # Rotate frame vthresh = np.rot90(np.rot90(vthresh)) # Rotate frame

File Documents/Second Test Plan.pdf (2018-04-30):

# Memo

To: | Professor Pisano, Professor Alshaykh, Professor Hirsch
From: | Christopher Liao, Anton Paquin, Jeffrey Lin, Eduardo Portet, Aviva Englander
Team: | 15
Date: | 2/13/18

Subject: Secondary Testing

### 1.0 Tracking Method 1: Tracking with one photodiode

1.1 Description of Test
In this test we will test tracking using one photodiode. The laser will make a circle to catch the photodiode when the signal is lost. When a point of the circle crosses the photodiode, we will try to center the laser onto the photodiode. As the photodiode moves around, there will be a circle encasing the photodiode.

1.2 Significance of Test
Tracking is the main problem in this project, and also the most difficult part. This tracking algorithm requires us to accurately predict when and where along the circle the laser has hit the photodiode so we can center the laser on the target. In order to do so, we would have to know the delay in our communication. We wanted to experiment with various tracking algorithms and see which one would suit our project the best.

1.3 Equipment and Setup
Single photodiode connected to an Arduino Leonardo via Analog Pin. Pair of NRF24L01 2.4GHz transreceivers each connected to a Arduino Leonardo, one with the photodiode array, the other with the base station. Arduino on the base station connected to a Particle Photon that is responsible for controlling the MEMS Mirror that is reflecting the laser.

1.4 Data Collection
The data will be serial prints from our microcontrollers.

1.5 Measurable Criteria

The metric for measuring success of our test would be if the circle can accurately follow the photodiode in every direction. In addition we will be measuring how far away and at approximately what speed the algorithm works.

### 2.0 Tracking Method 2: Tracking with five photodiodes

2.1 Description of Test
In this test we will demonstrate a rudimentary laser tracking mechanism. This test will use a laser (always on) being pointed with a MEMS mirror and a cluster of 5 photodiodes as the receiver. The photodiodes are arranged in a cross configuration. As the receptor moves left and right or up and down, the laser should be able to follow it.

The MEMS is programmed to move at a constant speed when it is not pointing at the target. When the laser hits the left photodiode, an interrupt is triggered and the MEMS changes its direction to move right. When the laser hits the right photodiode, an interrupt is triggered and the MEMS turns left. Similar interrupts are programmed for the up and down photodiodes. This test is an improvement upon the testing done last semester, since the laser will not move when it is directly hitting the target, so the tracking algorithm is slightly more stable. There are three main disadvantages of this tracking algorithm:
- We do not change the speed at which the laser moves when the target is lost, so the tracking will fail when the target is moving faster than the hard-coded speed of the laser.
- This algorithm could be improved if we program it to follow the target based on its past behavior (using a Kalman Filter for instance).
- There is no way to recover when we lose track of the target.

2.2 Significance of Test
As mentioned before, tracking is the main problem in this project. While the tracking setup demonstrated during this test is primitive, it is a good base to build more sophisticated tracking mechanisms upon. This test demonstrates our ability to control the laser with the MEMS.

This simple tracking algorithm gives a useful baseline to build upon for more sophisticated tracking methods.

2.3 Equipment and Setup
5 photodiodes in a cross configuration connected to an Arduino Leonardo via Analog Pins. Pair of NRF24L01 2.4GHz transreceivers each connected to a Arduino Leonardo, one with the photodiode array, the other with the base station. Arduino connected to a Particle Photon that is responsible for controlling the MEMS Mirror.

2.4 Data Collection
The data will be serial prints from our microcontrollers.

2.5 Measurable Criteria
The metric for measuring success of our test would be to approximate the maximum speed at which the laser still reliably follow the photodiode array. In addition we will be testing how far away the tracking algorithm works.

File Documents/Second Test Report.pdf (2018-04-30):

To: | Professor Pisano, Professor Alshaykh, Professor Hirsch
From: | Christopher Liao, Anton Paquin, Jeffrey Lin, Eduardo Portet, Aviva Englander
Team: | 15 - Laser Trac
Date: | 02/13/18

Subject: Second Deliverable Test Report

## 1. Project Objective

## 1.1. The overall objective of our project is to create an optical based tracking and communication system from a ground station to a UAV, allowing users to interact

with their vehicles without using Radio Frequency communication.

## 2. Test Objective and Significance

2.1. This test was significant because it demonstrated our ability to track the sensor,

## which is a fundamental component of our project. We demonstrated our closed loop control system, which included two wireless links -- the laser-to-sensor

component and the RF feedback signal.

2.2. This test focused on achieving a rough example of a tracking mechanism. With this test we demonstrated an ability to track an object with a laser while utilizing a photodiode array in the way we hope to for our final project. We successfully demonstrated a single-photodiode, 2-dimensional tracking system which could follow the array at a reasonable speed. The most important part of this test is how we incorporated the photodiode array into the tracking process. This is a

technique we hope to use in our final solution to the laser tracking problem.

## 3. Equipment and Setup

## 3.1. Receiver Circuit

This is the main hardware component of of our project.


## The photodiode circuit is tiled 16 times in our sensor array. Each output is treated as a single analog value, which is pulled low when the photodiode detects the presence of a

laser.
The LED in our circuit provides visual feedback for which signal is currently active.

## These indicators showed that 13 of the 16 circuit elements worked reliably, and 3 appeared to have broken photodiodes. We will fix this problem by replacing the failing

units as they are detected in future versions of the circuit.

## In our tests, we used (algorithm 1) 5 photodiodes and (algorithm 2) 1 photodiode, so the

missing signals were not a problem.

## 3.2. Tracking Algorithm I

## The first tracking algorithm is an extension of the naive tracking algorithm from first deliverable testing from one dimension to two dimensions. In this test we demonstrated a rudimentary tracking mechanism. A laser is pointed with a MEMS mirror at a cluster of 5

photodiodes on the receiver. The five photodiodes are arranged in a cross configuration.

## We demonstrated that as the receptor moves left and right or up and down, the laser is

able to follow.

## The MEMS is programmed to move at a constant speed when it is not pointing at the target. When the laser hits the left photodiode, an interrupt is triggered and the MEMS

changes its direction to move right. When the laser hits the right photodiode, an interrupt
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

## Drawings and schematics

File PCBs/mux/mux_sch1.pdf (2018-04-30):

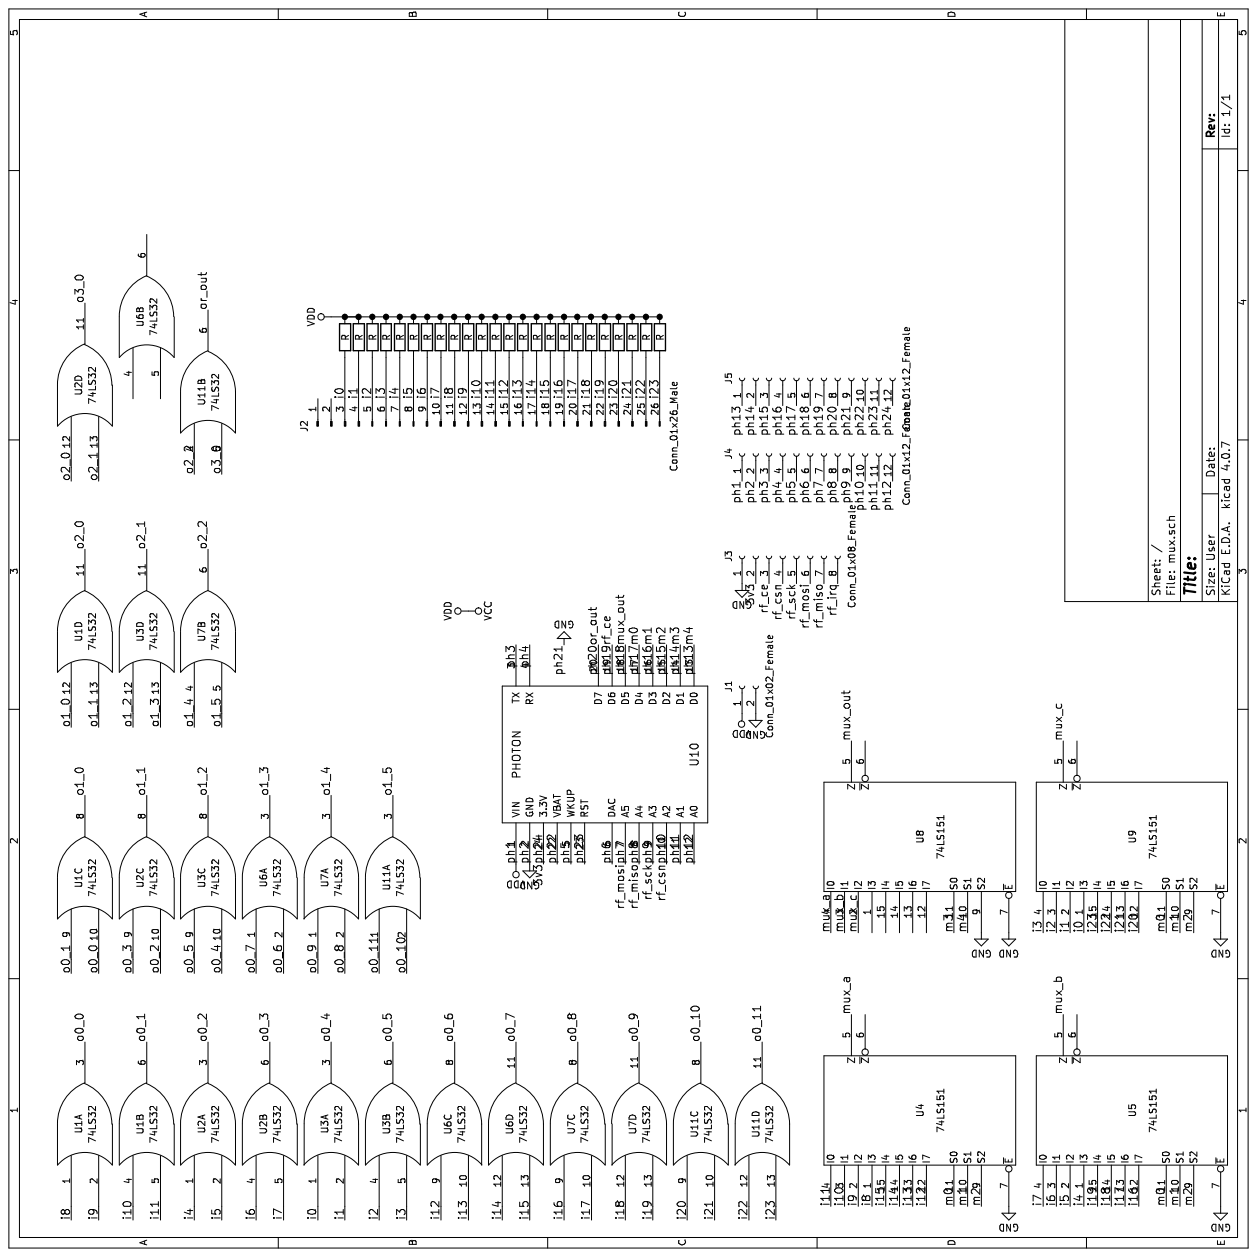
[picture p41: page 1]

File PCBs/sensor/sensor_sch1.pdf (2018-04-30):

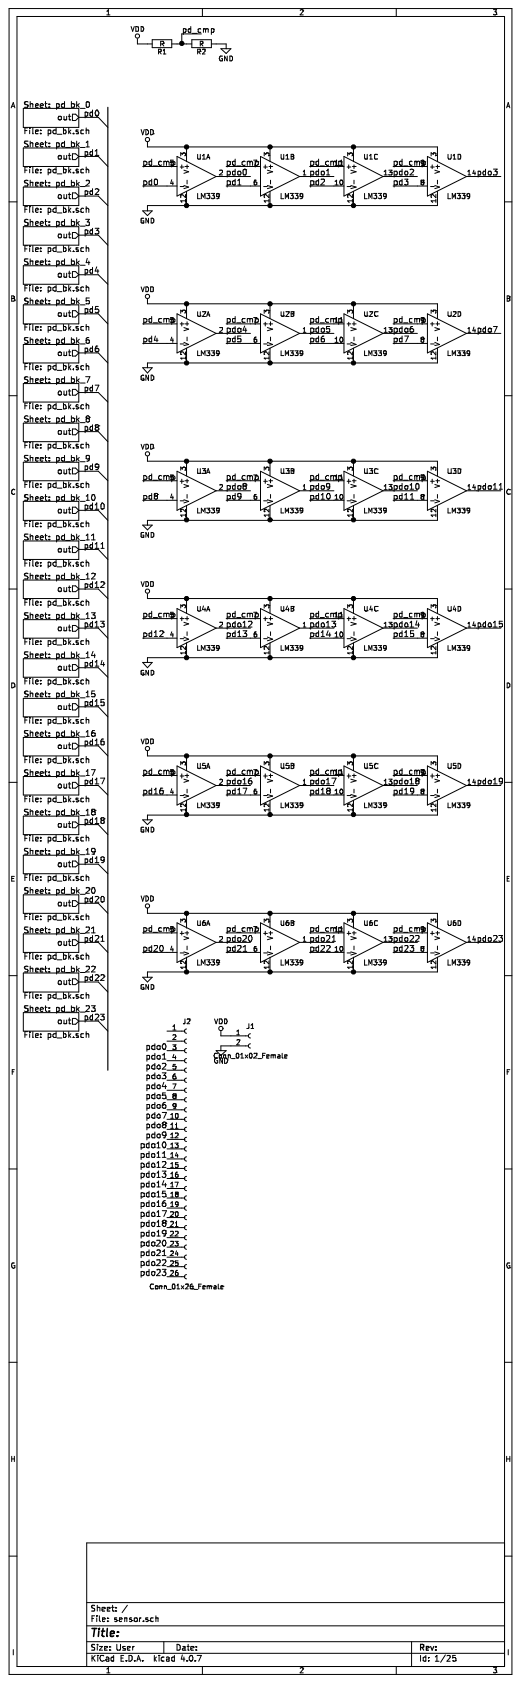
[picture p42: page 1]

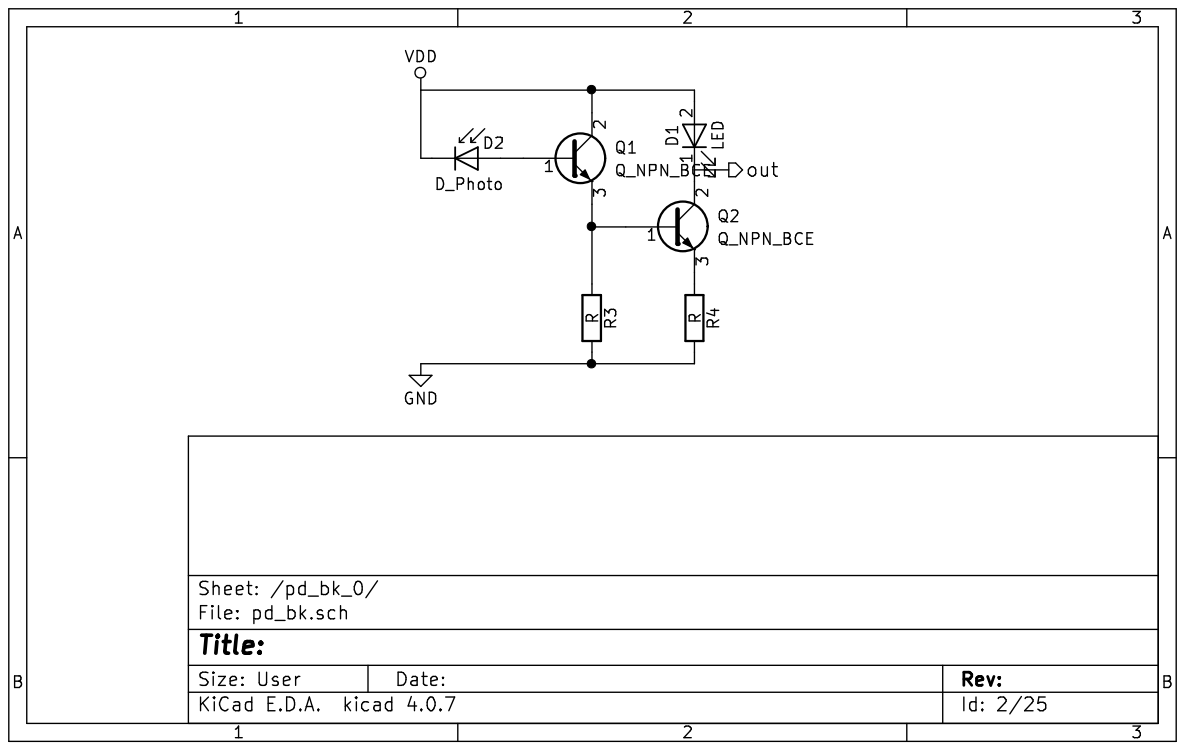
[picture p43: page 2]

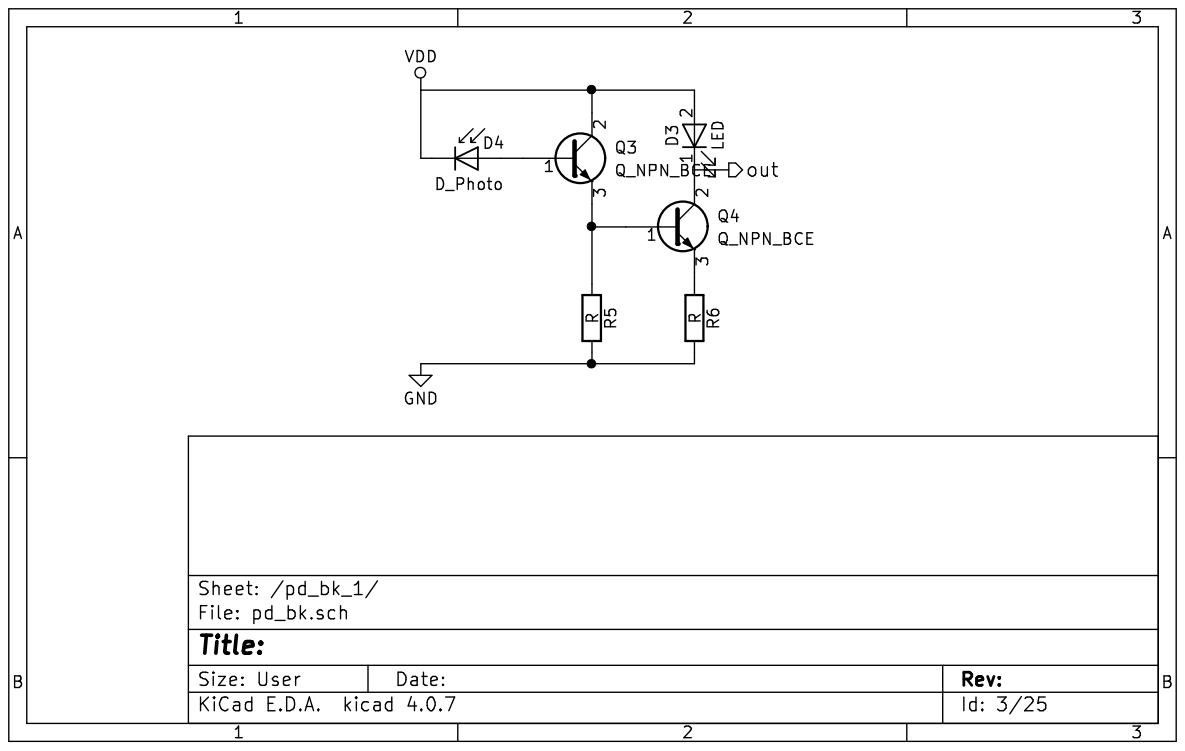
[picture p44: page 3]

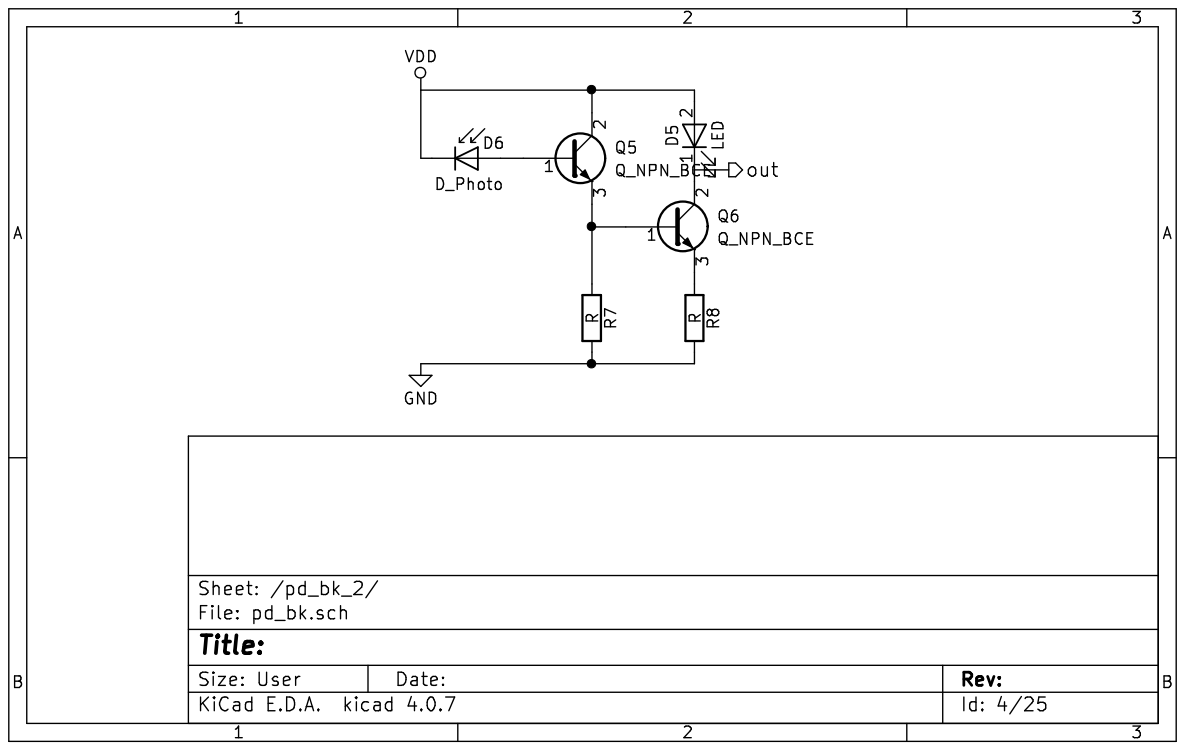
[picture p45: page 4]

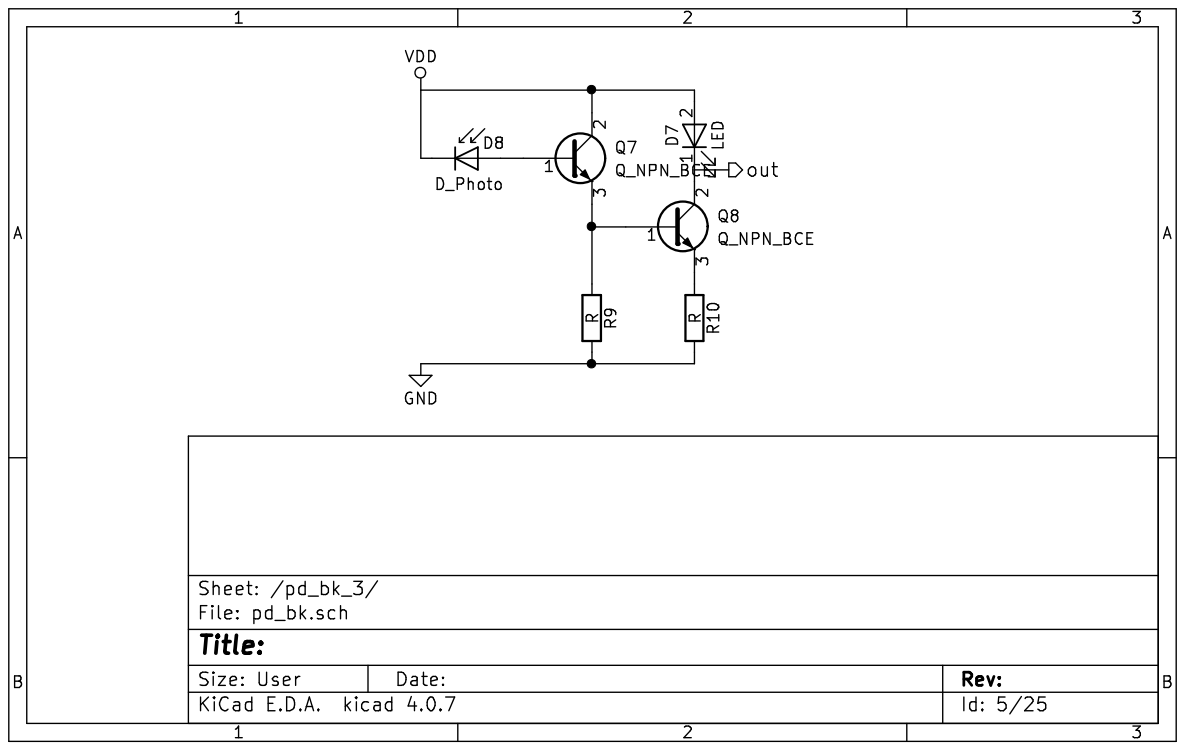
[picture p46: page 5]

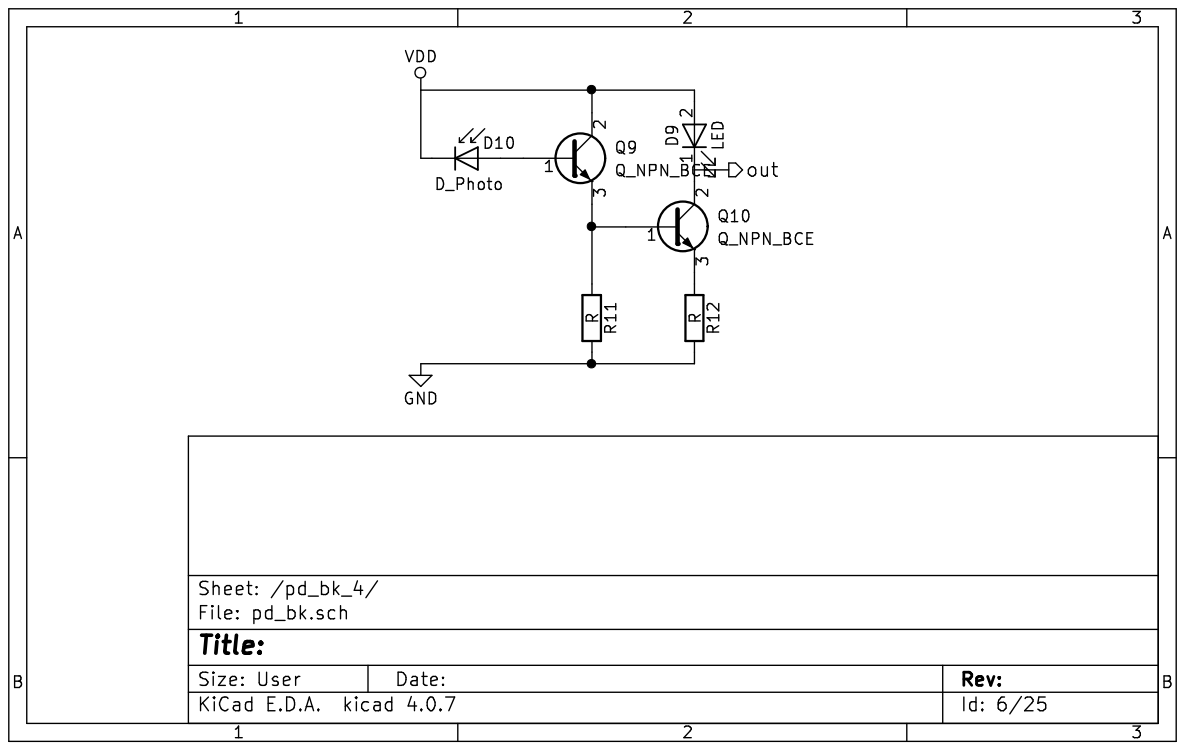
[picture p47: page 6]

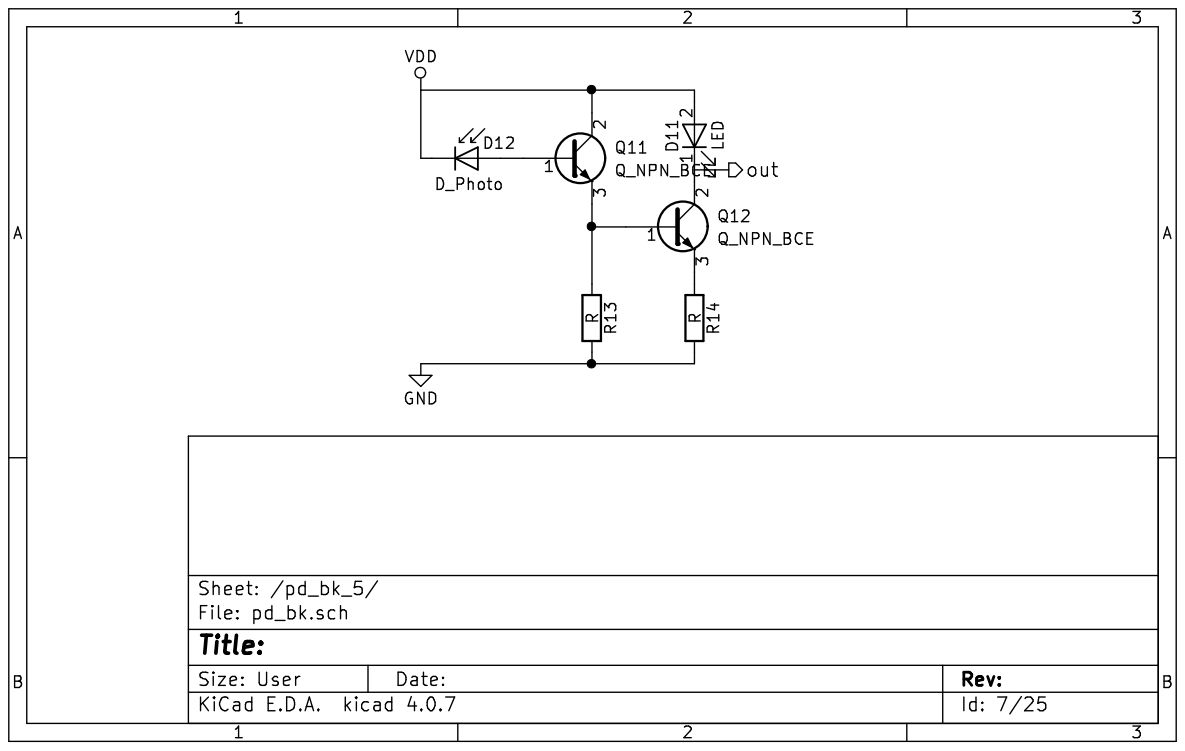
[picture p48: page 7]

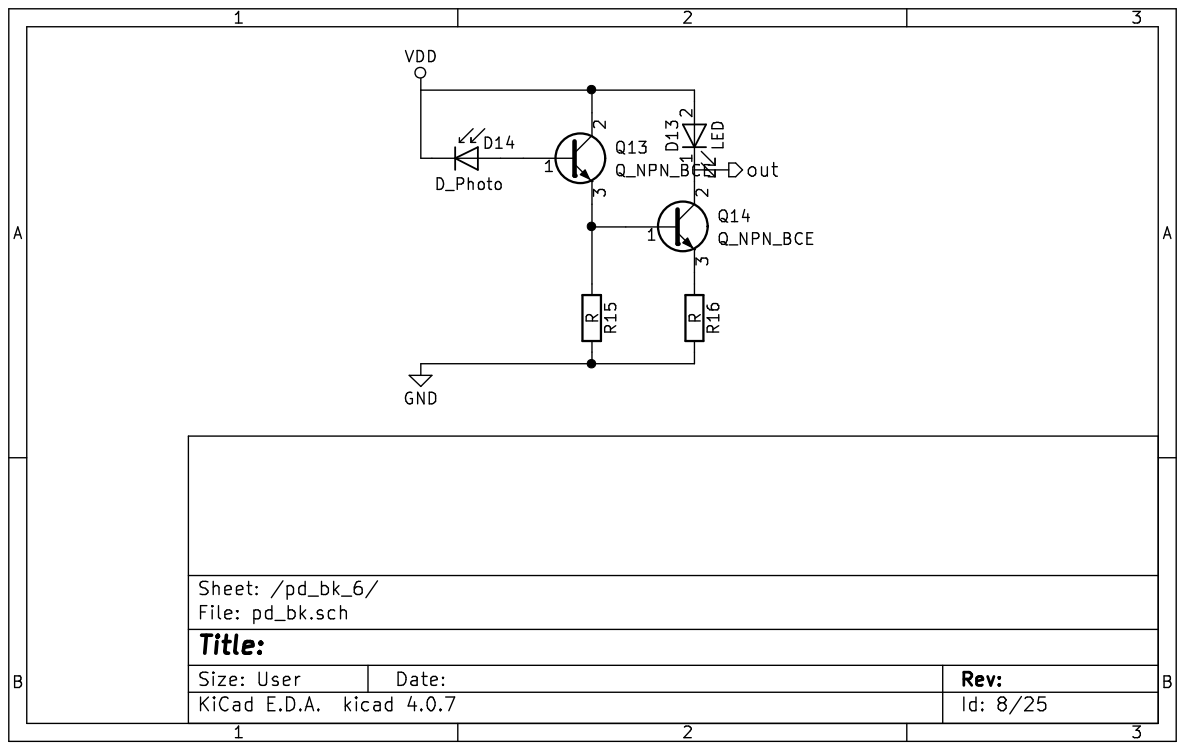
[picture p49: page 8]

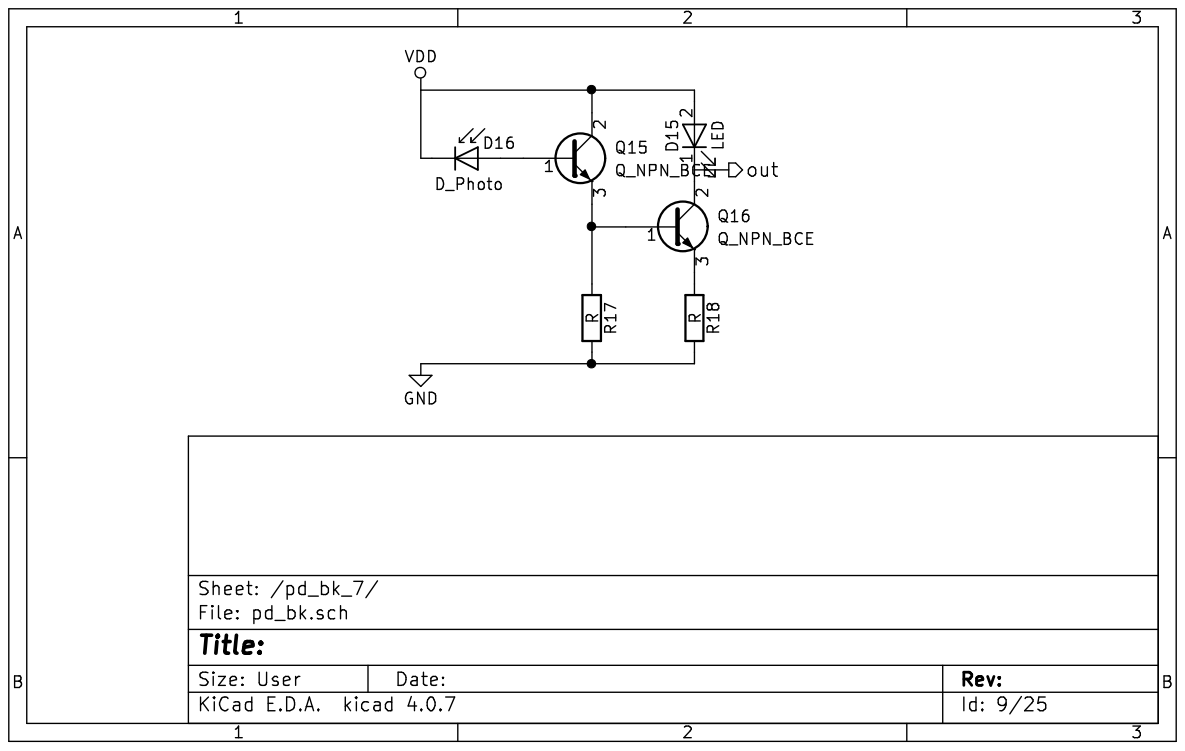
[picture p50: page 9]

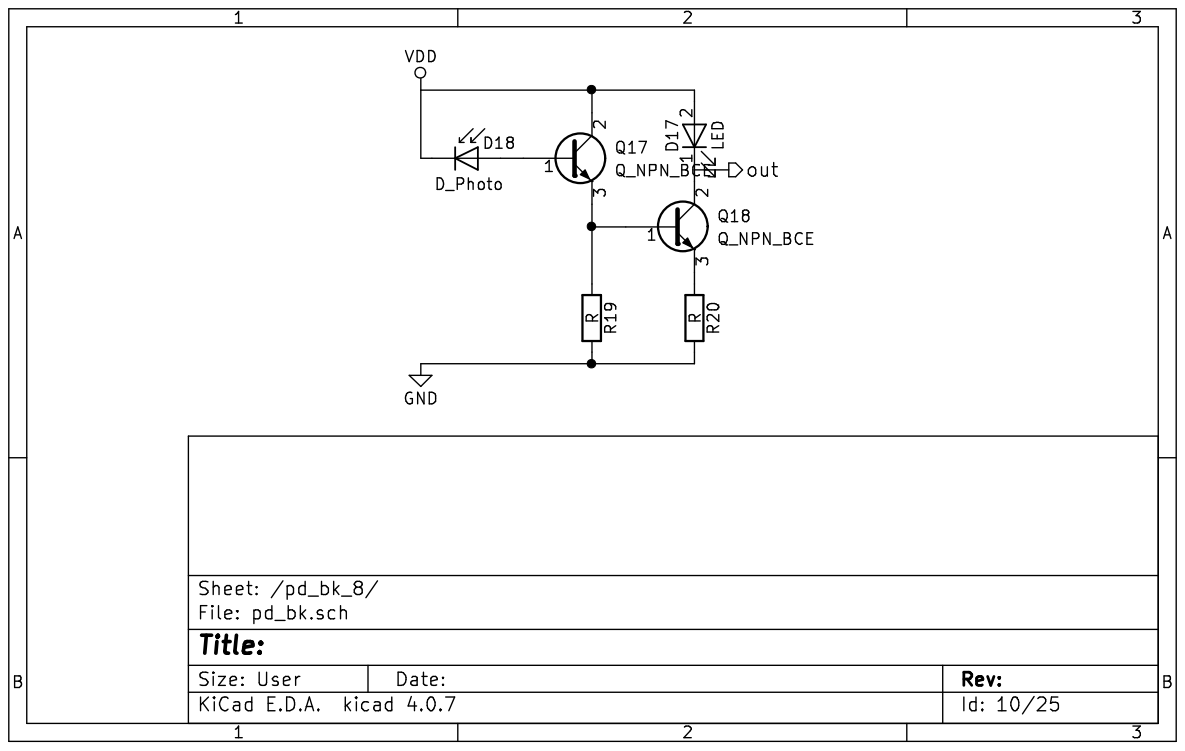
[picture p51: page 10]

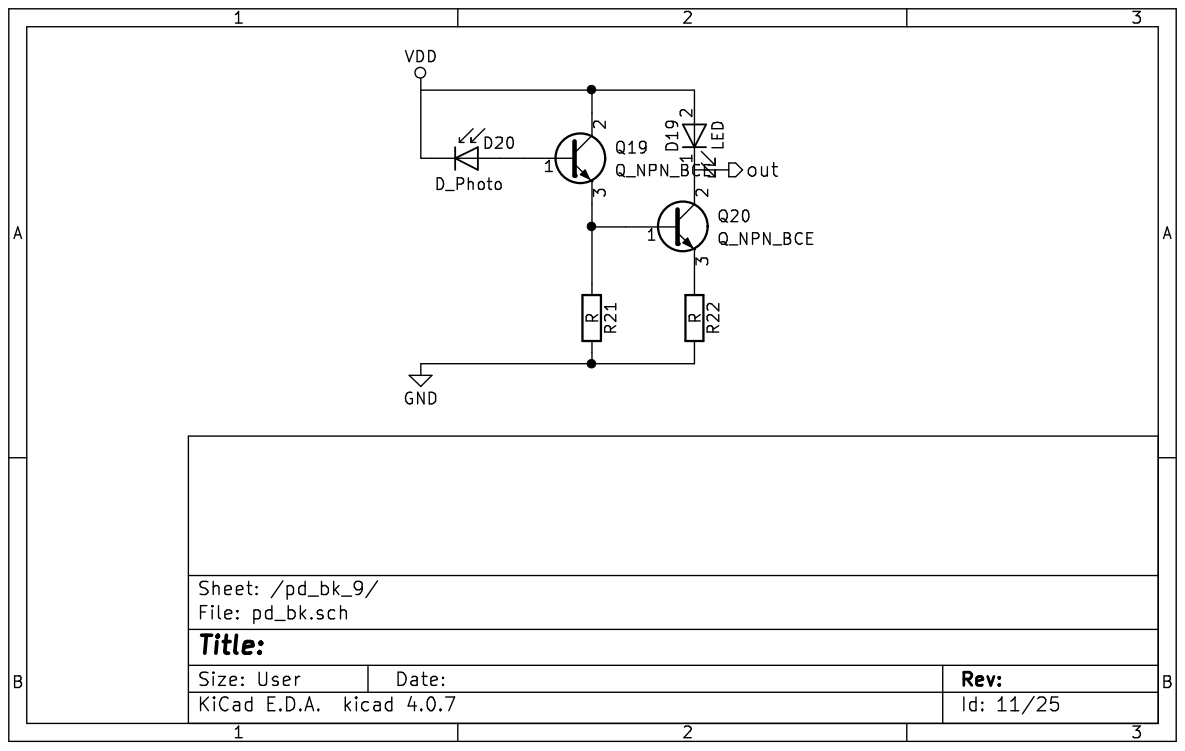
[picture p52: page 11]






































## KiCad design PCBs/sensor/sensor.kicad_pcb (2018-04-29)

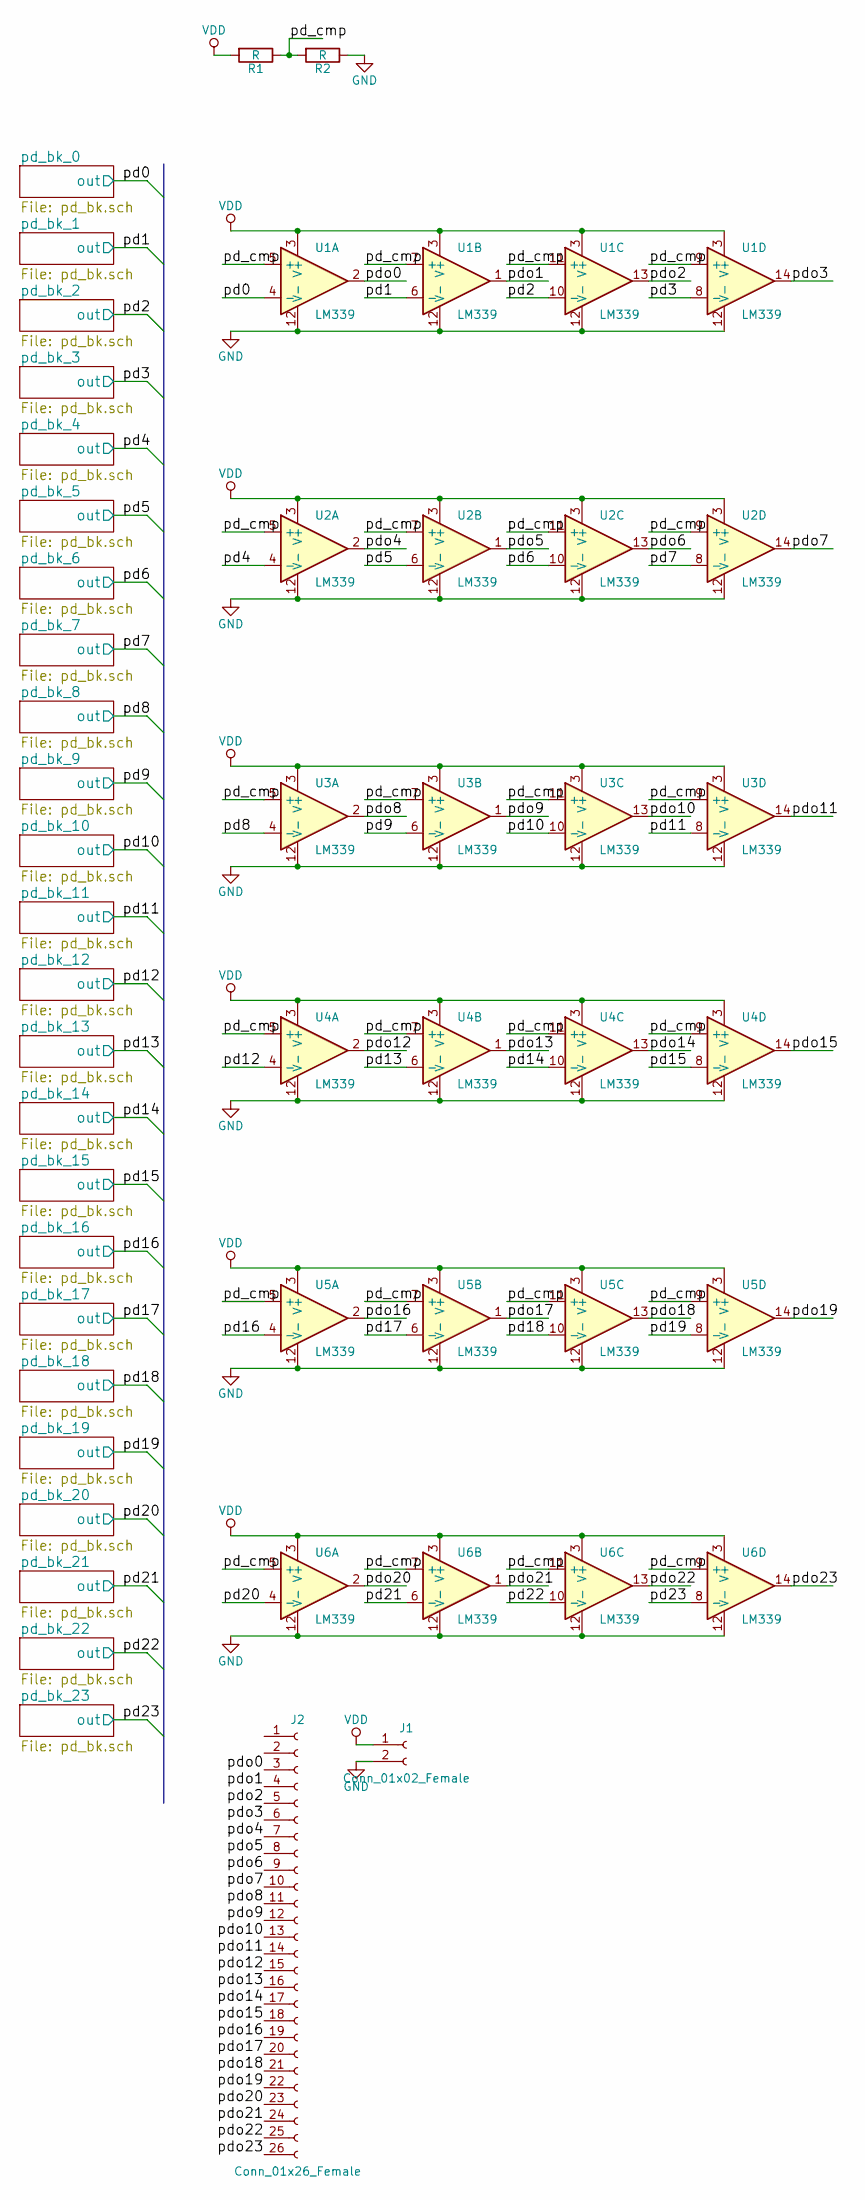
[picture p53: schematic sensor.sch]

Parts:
J1: Conn_01x02_Female; Pin_Header_Straight_1x02_Pitch2.54mm
J2: Conn_01x26_Female; Pin_Header_Straight_2x13_Pitch2.54mm
R1, R2: R; R_Axial_DIN0207_L6.3mm_D2.5mm_P2.54mm_Vertical
U1, U2, U3, U4, U5, U6: LM339; SOIC-14_3.9x8.7mm_Pitch1.27mm

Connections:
/pd0: U1.4 (-); also elsewhere on the board
/pd1: U1.6 (-); also elsewhere on the board
/pd2: U1.10 (-); also elsewhere on the board
/pd3: U1.8 (-); also elsewhere on the board
/pd4: U2.4 (-); also elsewhere on the board
/pd5: U2.6 (-); also elsewhere on the board
/pd6: U2.10 (-); also elsewhere on the board
/pd7: U2.8 (-); also elsewhere on the board
/pd8: U3.4 (-); also elsewhere on the board
/pd9: U3.6 (-); also elsewhere on the board
/pd10: U3.10 (-); also elsewhere on the board
/pd11: U3.8 (-); also elsewhere on the board
/pd12: U4.4 (-); also elsewhere on the board
/pd13: U4.6 (-); also elsewhere on the board
/pd14: U4.10 (-); also elsewhere on the board
/pd15: U4.8 (-); also elsewhere on the board
/pd16: U5.4 (-); also elsewhere on the board
/pd17: U5.6 (-); also elsewhere on the board
/pd18: U5.10 (-); also elsewhere on the board
/pd19: U5.8 (-); also elsewhere on the board
/pd20: U6.4 (-); also elsewhere on the board
/pd21: U6.6 (-); also elsewhere on the board
/pd22: U6.10 (-); also elsewhere on the board
/pd23: U6.8 (-); also elsewhere on the board
/pd_cmp: R1.1, R2.2, U1.5 (+), U1.7 (+), U1.9 (+), U1.11 (+), U2.5 (+), U2.7 (+), U2.9 (+), U2.11 (+), U3.5 (+), U3.7 (+), U3.9 (+), U3.11 (+), U4.5 (+), U4.7 (+), U4.9 (+), U4.11 (+), U5.5 (+), U5.7 (+), U5.9 (+), U5.11 (+), U6.5 (+), U6.7 (+), U6.9 (+), U6.11 (+)
/pdo0: J2.3, U1.2
/pdo1: J2.4, U1.1
/pdo2: J2.5, U1.13
/pdo3: J2.6, U1.14
/pdo4: J2.7, U2.2
/pdo5: J2.8, U2.1
/pdo6: J2.9, U2.13
/pdo7: J2.10, U2.14
/pdo8: J2.11, U3.2
/pdo9: J2.12, U3.1
/pdo10: J2.13, U3.13
/pdo11: J2.14, U3.14
/pdo12: J2.15, U4.2
/pdo13: J2.16, U4.1
/pdo14: J2.17, U4.13
/pdo15: J2.18, U4.14
/pdo16: J2.19, U5.2
/pdo17: J2.20, U5.1
/pdo18: J2.21, U5.13
/pdo19: J2.22, U5.14
/pdo20: J2.23, U6.2
/pdo21: J2.24, U6.1
/pdo22: J2.25, U6.13
/pdo23: J2.26, U6.14
GND: J1.2, R2.1, U1.12 (V-), U2.12 (V-), U3.12 (V-), U4.12 (V-), U5.12 (V-), U6.12 (V-); also elsewhere on the board
VDD: J1.1, R1.2, U1.3 (V+), U2.3 (V+), U3.3 (V+), U4.3 (V+), U5.3 (V+), U6.3 (V+); also elsewhere on the board

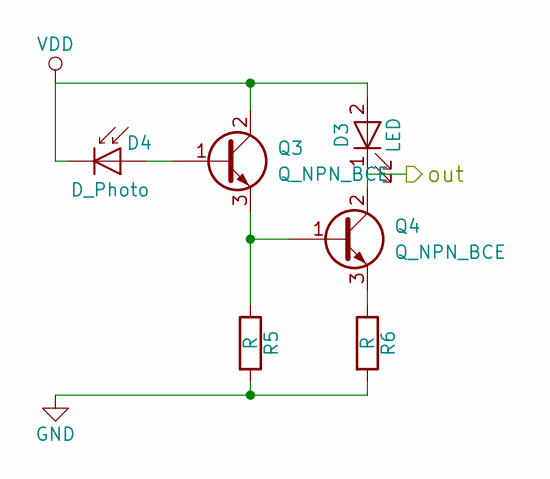
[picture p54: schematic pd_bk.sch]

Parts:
D1: LED; LED_1206_HandSoldering
D2: D_Photo; LED_1206
Q1, Q2: Q_NPN_BCE; SOT-23_Handsoldering
R3, R4: R; R_1206_HandSoldering

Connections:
/pd0: D1.1 (K), Q2.2 (C); also elsewhere on the board
GND: R3.2, R4.2; also elsewhere on the board
unnamed: D2.2 (A), Q1.1 (B)
unnamed: Q1.3 (E), Q2.1 (B), R3.1
unnamed: Q2.3 (E), R4.1
VDD: D1.2 (A), D2.1 (K), Q1.2 (C); also elsewhere on the board

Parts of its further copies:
D3, D5, D7, D9, D11, D13, D15, D17, D19, D21, D23, D25, D27, D29, D31, D33, D35, D37, D39, D41, D43, D45, D47, D49: LED; LED_1206_HandSoldering
D4, D6, D8, D10, D12, D14, D16, D18, D20, D22, D24, D26, D28, D30, D32, D34, D36, D38, D40, D42, D44, D46, D48, D50: D_Photo; LED_1206
Q3, Q4, Q5, Q6, Q7, Q8, Q9, Q10, Q11, Q12, Q13, Q14, Q15, Q16, Q17, Q18, Q19, Q20, Q21, Q22, Q23, Q24, Q25, Q26, Q27, Q28, Q29, Q30, Q31, Q32, Q33, Q34, Q35, Q36, Q37, Q38, Q39, Q40, Q41, Q42, Q43, Q44, Q45, Q46, Q47, Q48, Q49, Q50: Q_NPN_BCE; SOT-23_Handsoldering
R5, R6, R7, R8, R9, R10, R11, R12, R13, R14, R15, R16, R17, R18, R19, R20, R21, R22, R23, R24, R25, R26, R27, R28, R29, R30, R31, R32, R33, R34, R35, R36, R37, R38, R39, R40, R41, R42, R43, R44, R45, R46, R47, R48, R49, R50, R51, R52: R; R_1206_HandSoldering

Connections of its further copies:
/pd1: D3.1 (K), Q4.2 (C); also elsewhere on the board
/pd2: D5.1 (K), Q6.2 (C); also elsewhere on the board
/pd3: D7.1 (K), Q8.2 (C); also elsewhere on the board
/pd4: D9.1 (K), Q10.2 (C); also elsewhere on the board
/pd5: D11.1 (K), Q12.2 (C); also elsewhere on the board
/pd6: D13.1 (K), Q14.2 (C); also elsewhere on the board
/pd7: D15.1 (K), Q16.2 (C); also elsewhere on the board
/pd8: D17.1 (K), Q18.2 (C); also elsewhere on the board
/pd9: D19.1 (K), Q20.2 (C); also elsewhere on the board
/pd10: D21.1 (K), Q22.2 (C); also elsewhere on the board
/pd11: D23.1 (K), Q24.2 (C); also elsewhere on the board
/pd12: D25.1 (K), Q26.2 (C); also elsewhere on the board
/pd13: D27.1 (K), Q28.2 (C); also elsewhere on the board
/pd14: D29.1 (K), Q30.2 (C); also elsewhere on the board
/pd15: D31.1 (K), Q32.2 (C); also elsewhere on the board
/pd16: D33.1 (K), Q34.2 (C); also elsewhere on the board
/pd17: D35.1 (K), Q36.2 (C); also elsewhere on the board
/pd18: D37.1 (K), Q38.2 (C); also elsewhere on the board
/pd19: D39.1 (K), Q40.2 (C); also elsewhere on the board
/pd20: D41.1 (K), Q42.2 (C); also elsewhere on the board
/pd21: D43.1 (K), Q44.2 (C); also elsewhere on the board
/pd22: D45.1 (K), Q46.2 (C); also elsewhere on the board
/pd23: D47.1 (K), Q48.2 (C); also elsewhere on the board
GND: R5.2, R6.2, R7.2, R8.2, R9.2, R10.2, R11.2, R12.2, R13.2, R14.2, R15.2, R16.2, R17.2, R18.2, R19.2, R20.2, R21.2, R22.2, R23.2, R24.2, R25.2, R26.2, R27.2, R28.2, R29.2, R30.2, R31.2, R32.2, R33.2, R34.2, R35.2, R36.2, R37.2, R38.2, R39.2, R40.2, R41.2, R42.2, R43.2, R44.2, R45.2, R46.2, R47.2, R48.2, R49.2, R50.2; also elsewhere on the board
unnamed: D4.2 (A), Q3.1 (B)
unnamed: D6.2 (A), Q5.1 (B)
unnamed: D8.2 (A), Q7.1 (B)
unnamed: D10.2 (A), Q9.1 (B)
unnamed: D12.2 (A), Q11.1 (B)
unnamed: D14.2 (A), Q13.1 (B)
unnamed: D16.2 (A), Q15.1 (B)
unnamed: D18.2 (A), Q17.1 (B)
unnamed: D20.2 (A), Q19.1 (B)
unnamed: D22.2 (A), Q21.1 (B)
unnamed: D24.2 (A), Q23.1 (B)
unnamed: D26.2 (A), Q25.1 (B)
unnamed: D28.2 (A), Q27.1 (B)
unnamed: D30.2 (A), Q29.1 (B)
unnamed: D32.2 (A), Q31.1 (B)
unnamed: D34.2 (A), Q33.1 (B)
unnamed: D36.2 (A), Q35.1 (B)
unnamed: D38.2 (A), Q37.1 (B)
unnamed: D40.2 (A), Q39.1 (B)
unnamed: D42.2 (A), Q41.1 (B)
unnamed: D44.2 (A), Q43.1 (B)
unnamed: D46.2 (A), Q45.1 (B)
unnamed: D48.2 (A), Q47.1 (B)
unnamed: Q3.3 (E), Q4.1 (B), R5.1
unnamed: Q4.3 (E), R6.1
unnamed: Q5.3 (E), Q6.1 (B), R7.1
unnamed: Q6.3 (E), R8.1
unnamed: Q7.3 (E), Q8.1 (B), R9.1
unnamed: Q8.3 (E), R10.1
unnamed: Q9.3 (E), Q10.1 (B), R11.1
unnamed: Q10.3 (E), R12.1
unnamed: Q11.3 (E), Q12.1 (B), R13.1
unnamed: Q12.3 (E), R14.1
unnamed: Q13.3 (E), Q14.1 (B), R15.1
unnamed: Q14.3 (E), R16.1
unnamed: Q15.3 (E), Q16.1 (B), R17.1
unnamed: Q16.3 (E), R18.1
unnamed: Q17.3 (E), Q18.1 (B), R19.1
unnamed: Q18.3 (E), R20.1
unnamed: Q19.3 (E), Q20.1 (B), R21.1
unnamed: Q20.3 (E), R22.1
unnamed: Q21.3 (E), Q22.1 (B), R23.1
unnamed: Q22.3 (E), R24.1
unnamed: Q23.3 (E), Q24.1 (B), R25.1
unnamed: Q24.3 (E), R26.1
unnamed: Q25.3 (E), Q26.1 (B), R27.1
unnamed: Q26.3 (E), R28.1
unnamed: Q27.3 (E), Q28.1 (B), R29.1
unnamed: Q28.3 (E), R30.1
unnamed: Q29.3 (E), Q30.1 (B), R31.1
unnamed: Q30.3 (E), R32.1
unnamed: Q31.3 (E), Q32.1 (B), R33.1
unnamed: Q32.3 (E), R34.1
unnamed: Q33.3 (E), Q34.1 (B), R35.1
unnamed: Q34.3 (E), R36.1
unnamed: Q35.3 (E), Q36.1 (B), R37.1
unnamed: Q36.3 (E), R38.1
unnamed: Q37.3 (E), Q38.1 (B), R39.1
unnamed: Q38.3 (E), R40.1
unnamed: Q39.3 (E), Q40.1 (B), R41.1
unnamed: Q40.3 (E), R42.1
unnamed: Q41.3 (E), Q42.1 (B), R43.1
unnamed: Q42.3 (E), R44.1
unnamed: Q43.3 (E), Q44.1 (B), R45.1
unnamed: Q44.3 (E), R46.1
unnamed: Q45.3 (E), Q46.1 (B), R47.1
unnamed: Q46.3 (E), R48.1
unnamed: Q47.3 (E), Q48.1 (B), R49.1
unnamed: Q48.3 (E), R50.1
VDD: D3.2 (A), D4.1 (K), D5.2 (A), D6.1 (K), D7.2 (A), D8.1 (K), D9.2 (A), D10.1 (K), D11.2 (A), D12.1 (K), D13.2 (A), D14.1 (K), D15.2 (A), D16.1 (K), D17.2 (A), D18.1 (K), D19.2 (A), D20.1 (K), D21.2 (A), D22.1 (K), D23.2 (A), D24.1 (K), D25.2 (A), D26.1 (K), D27.2 (A), D28.1 (K), D29.2 (A), D30.1 (K), D31.2 (A), D32.1 (K), D33.2 (A), D34.1 (K), D35.2 (A), D36.1 (K), D37.2 (A), D38.1 (K), D39.2 (A), D40.1 (K), D41.2 (A), D42.1 (K), D43.2 (A), D44.1 (K), D45.2 (A), D46.1 (K), D47.2 (A), D48.1 (K), Q3.2 (C), Q5.2 (C), Q7.2 (C), Q9.2 (C), Q11.2 (C), Q13.2 (C), Q15.2 (C), Q17.2 (C), Q19.2 (C), Q21.2 (C), Q23.2 (C), Q25.2 (C), Q27.2 (C), Q29.2 (C), Q31.2 (C), Q33.2 (C), Q35.2 (C), Q37.2 (C), Q39.2 (C), Q41.2 (C), Q43.2 (C), Q45.2 (C), Q47.2 (C); also elsewhere on the board

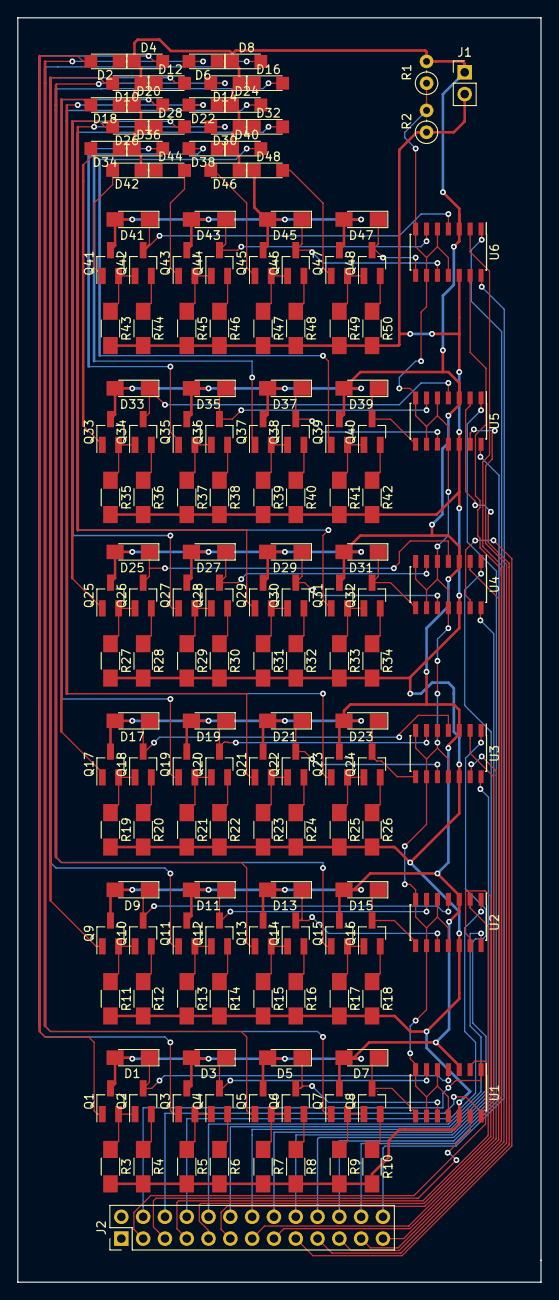
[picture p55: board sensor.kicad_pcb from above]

Board: 2 copper layers, 61.0 x 147.3 mm, 154 parts (0 on the bottom side), 123 nets.

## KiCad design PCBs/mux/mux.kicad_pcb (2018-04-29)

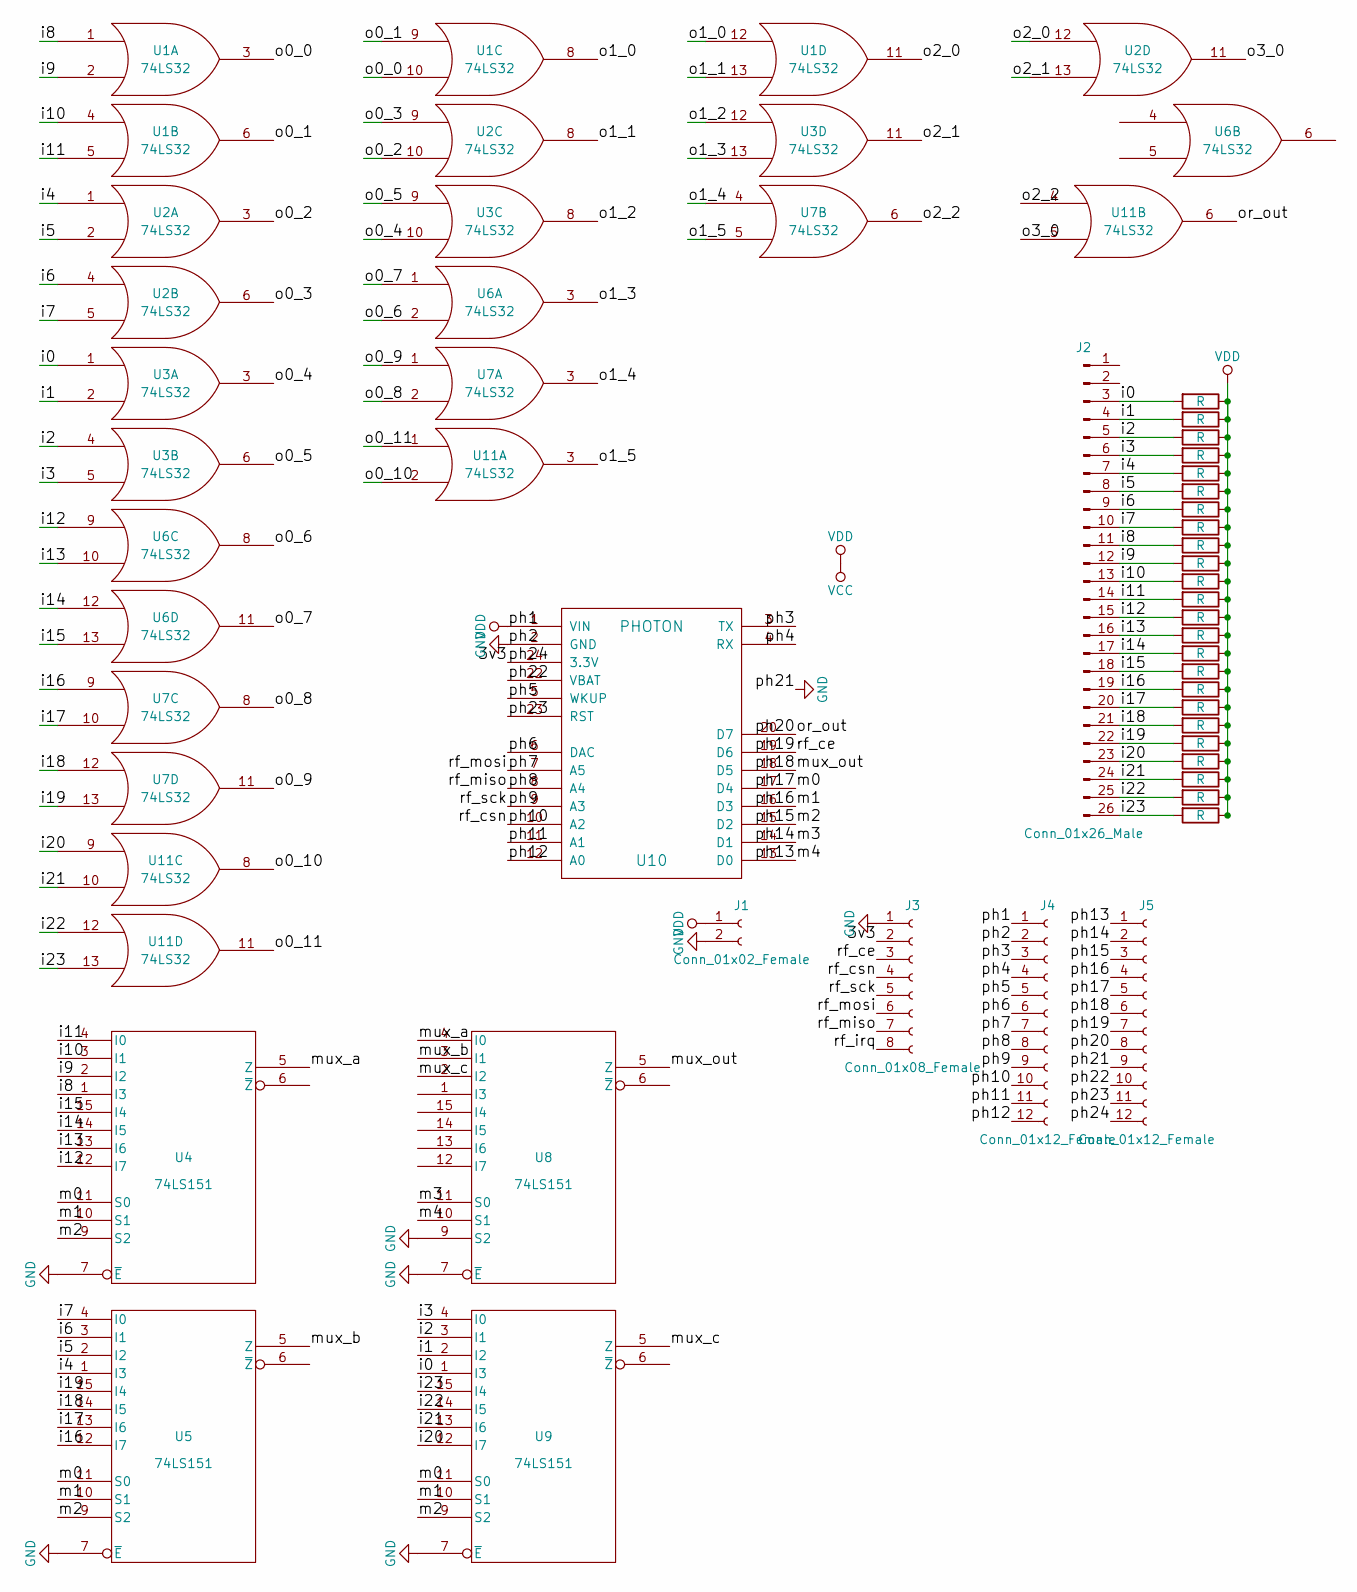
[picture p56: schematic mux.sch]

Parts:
J1: Conn_01x02_Female; Pin_Header_Straight_1x02_Pitch2.54mm
J2: Conn_01x26_Male; Pin_Header_Straight_2x13_Pitch2.54mm
J3: Conn_01x08_Female; Pin_Header_Straight_2x04_Pitch2.54mm
J4, J5: Conn_01x12_Female; Pin_Header_Straight_1x12_Pitch2.54mm
R1, R2, R3, R4, R5, R6, R7, R8, R9, R10, R11, R12, R13, R14, R15, R16, R17, R18, R19, R20, R21, R22, R23, R24: R; R_1206
U1, U2, U3, U6, U7, U11: 74LS32; SOIC-14_3.9x8.7mm_Pitch1.27mm
U4, U5, U8, U9: 74LS151; SOIC-16_3.9x9.9mm_Pitch1.27mm
U10: PHOTON

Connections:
/3v3: J3.2, J5.12, U10.24 (3.3V)
/i0: J2.3, R1.2, U3.1, U9.1 (I3)
/i1: J2.4, R2.2, U3.2, U9.2 (I2)
/i2: J2.5, R3.2, U3.4, U9.3 (I1)
/i3: J2.6, R4.2, U3.5, U9.4 (I0)
/i4: J2.7, R5.2, U2.1, U5.1 (I3)
/i5: J2.8, R6.2, U2.2, U5.2 (I2)
/i6: J2.9, R7.2, U2.4, U5.3 (I1)
/i7: J2.10, R8.2, U2.5, U5.4 (I0)
/i8: J2.11, R9.2, U1.1, U4.1 (I3)
/i9: J2.12, R10.2, U1.2, U4.2 (I2)
/i10: J2.13, R11.2, U1.4, U4.3 (I1)
/i11: J2.14, R12.2, U1.5, U4.4 (I0)
/i12: J2.15, R13.2, U4.12 (I7), U6.9
/i13: J2.16, R14.2, U4.13 (I6), U6.10
/i14: J2.17, R15.2, U4.14 (I5), U6.12
/i15: J2.18, R16.2, U4.15 (I4), U6.13
/i16: J2.19, R17.2, U5.12 (I7), U7.9
/i17: J2.20, R18.2, U5.13 (I6), U7.10
/i18: J2.21, R19.2, U5.14 (I5), U7.12
/i19: J2.22, R20.2, U5.15 (I4), U7.13
/i20: J2.23, R21.2, U9.12 (I7), U11.9
/i21: J2.24, R22.2, U9.13 (I6), U11.10
/i22: J2.25, R23.2, U9.14 (I5), U11.12
/i23: J2.26, R24.2, U9.15 (I4), U11.13
/m0: J5.5, U4.11 (S0), U5.11 (S0), U9.11 (S0), U10.17 (D4)
/m1: J5.4, U4.10 (S1), U5.10 (S1), U9.10 (S1), U10.16 (D3)
/m2: J5.3, U4.9 (S2), U5.9 (S2), U9.9 (S2), U10.15 (D2)
/m3: J5.2, U8.11 (S0), U10.14 (D1)
/m4: J5.1, U8.10 (S1), U10.13 (D0)
/mux_a: U4.5 (Z), U8.4 (I0)
/mux_b: U5.5 (Z), U8.3 (I1)
/mux_c: U8.2 (I2), U9.5 (Z)
/mux_out: J5.6, U8.5 (Z), U10.18 (D5)
/o0_0: U1.3, U1.10
/o0_1: U1.6, U1.9
/o0_2: U2.3, U2.10
/o0_3: U2.6, U2.9
/o0_4: U3.3, U3.10
/o0_5: U3.6, U3.9
/o0_6: U6.2, U6.8
/o0_7: U6.1, U6.11
/o0_8: U7.2, U7.8
/o0_9: U7.1, U7.11
/o0_10: U11.2, U11.8
/o0_11: U11.1, U11.11
/o1_0: U1.8, U1.12
/o1_1: U1.13, U2.8
/o1_2: U3.8, U3.12
/o1_3: U3.13, U6.3
/o1_4: U7.3, U7.4
/o1_5: U7.5, U11.3
/o2_0: U1.11, U2.12
/o2_1: U2.13, U3.11
/o2_2: U7.6, U11.4
/o3_0: U2.11, U11.5
/or_out: J5.8, U10.20 (D7), U11.6
/ph3: J4.3, U10.3 (TX)
/ph4: J4.4, U10.4 (RX)
/ph5: J4.5, U10.5 (WKUP)
/ph6: J4.6, U10.6 (DAC)
/ph7: J3.6, J4.7, U10.7 (A5)
/ph8: J3.7, J4.8, U10.8 (A4)
/ph9: J3.5, J4.9, U10.9 (A3)
/ph10: J3.4, J4.10, U10.10 (A2)
/ph11: J4.11, U10.11 (A1)
/ph12: J4.12, U10.12 (A0)
/ph19: J3.3, J5.7, U10.19 (D6)
/ph22: J5.10, U10.22 (VBAT)
/ph23: J5.11, U10.23 (RST)
/rf_irq: J3.8
GND: J1.2, J3.1, J4.2, J5.9, U1.7 (GND), U2.7 (GND), U3.7 (GND), U4.7 (~E), U4.8 (GND), U5.7 (~E), U5.8 (GND), U6.7 (GND), U7.7 (GND), U8.7 (~E), U8.8 (GND), U8.9 (S2), U9.7 (~E), U9.8 (GND), U10.2 (GND), U11.7 (GND)
VCC: J1.1, J4.1, R1.1, R2.1, R3.1, R4.1, R5.1, R6.1, R7.1, R8.1, R9.1, R10.1, R11.1, R12.1, R13.1, R14.1, R15.1, R16.1, R17.1, R18.1, R19.1, R20.1, R21.1, R22.1, R23.1, R24.1, U1.14 (VCC), U2.14 (VCC), U3.14 (VCC), U4.16 (VCC), U5.16 (VCC), U6.14 (VCC), U7.14 (VCC), U8.16 (VCC), U9.16 (VCC), U10.1 (VIN), U11.14 (VCC)

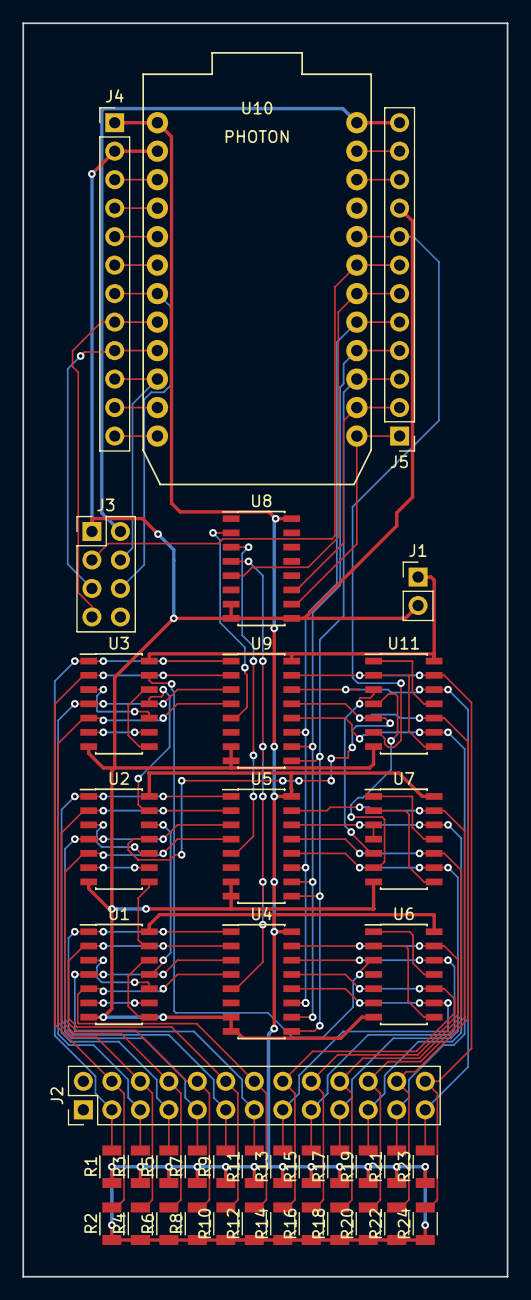
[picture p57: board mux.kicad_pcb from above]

Board: 2 copper layers, 43.2 x 111.8 mm, 41 parts (1 on the bottom side), 72 nets.

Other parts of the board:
LOGO: LOGO

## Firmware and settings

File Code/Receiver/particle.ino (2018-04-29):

SYSTEM_MODE(MANUAL);

#include <SPI.h>
#include "nRF24L01.h"
#include "particle-rf24.h"
#include "math.h"

const int enable_pin  = D7; // (pin 1) pin to enable MEMS output
const int fclk_pin    = D0; // (pin 2) pin to set frequency of Bessel low pass filter

const int ss          = A2; // SS or CSN for MEMS
const int ss_radio    = D5; // SS or CSN for radio
const int sck         = A3; // (pin 6)
const int mosi        = A5; // (pin 4)
                            // Gnd (pin 3 and pin 5)
                            // +5V (pin 7)
const int ce          = D6; // to set TX or RX modes for radio

const int mon_pin     = WKP; // WKP is monitor pin for Lidar

const int azimuth_pin = TX;
const int pitch_pin   = RX;

RF24 radio(ce, ss_radio); // CE, CSN
const byte address[][6] = {"00001","00002"};
int8_t radio_data[2] = {0,0};

int full_reset                  = 2621441; //Initialization to set up DAC
int enable_internal_reference   = 3670017; //Initialization to set up DAC
int enable_all_dac_channels     = 2097167; // B00100000 00000000 00001111//Initialization to set up DAC
int enable_software_ldac        = 3145728; // B00110000 00000000 00000000 //Initialization to set up DAC
int disable_all_dac_channels    = 2097215; //Power Down

#define AD56X4_COMMAND_WRITE_INPUT_REGISTER             0 //B00000000 //Set the channel(s)'s input register.
#define AD56X4_COMMAND_UPDATE_DAC_REGISTER              8 //B00001000 //Update the DAC register (output the set voltage)
#define AD56X4_COMMAND_WRITE_INPUT_REGISTER_UPDATE_ALL  16 //B00010000 //Set channel/s's input register and then update all DAC registers from the input registers.

#define AD56X4_CHANNEL_A                               0 //B00000000
#define AD56X4_CHANNEL_B                               1 //B00000001
#define AD56X4_CHANNEL_C                               2 //B00000010
#define AD56X4_CHANNEL_D                               3 //B00000011
#define AD56X4_CHANNEL_ALL                             7 //B00000111

#define pi 3.1415926
#define BUF_SIZE 100

// commands to write to LDAC buffer, then at channel_D write to DAC register
int writecommand[]  = {AD56X4_COMMAND_WRITE_INPUT_REGISTER  | AD56X4_CHANNEL_A,
                       AD56X4_COMMAND_WRITE_INPUT_REGISTER  | AD56X4_CHANNEL_B,
                       AD56X4_COMMAND_WRITE_INPUT_REGISTER  | AD56X4_CHANNEL_C,
                       AD56X4_COMMAND_WRITE_INPUT_REGISTER_UPDATE_ALL  | AD56X4_CHANNEL_D
                     };

// Set mirror dependent values
int freq            = 650; // 650 Hz recommended cutoff frequency
int fclk_freq       = 60*freq; //39000;    // Recommended 650 Hz * 60 - do not change!!!!!!
double max_voltage  = 157;      // Datasheet spec - do not change!!!!!!
int bias_voltage    = 80;       // Datasheet spec - do not change!!!!!!
double analog_bias  = (bias_voltage*65535)/160 + 0.5;
int dig_bias        = (int) analog_bias;
int data;
int pitch_servo_pos   = 1800; // level
int azimuth_servo_pos = 1500; // midway point
int azimuth_ctl_i_acc = 0;
int azimuth_ctl_d_last = 0;
Servo pitch_servo, azimuth_servo;

// Required constants
volatile double difX, difY, incX, incY;
const double inc = 0.2;
int right = 0;
int up = 0;
double bufX[BUF_SIZE] = {};
double bufY[BUF_SIZE] = {};
int p = 0;
int q = 1;
int serial_counter = 0;
const double ki=0, kp=1, kd=0;

double pulseWidth=0.0; // radial distance
double az=0.0; // azimuth angle of laser
double el=0.0; // elevation angle of laser
double h=0.0; // sqrt(x^2+y^2)
double x=0.0;
double y=0.0;
double z=0.0;

void azimuth_write(int pos);
int azimuth_controller_update(double mems_pos);
void pitch_write(int pos);

void setup() {
  pinMode(enable_pin, OUTPUT);
  pinMode(fclk_pin, OUTPUT);
  pinMode(ss, OUTPUT);
  pinMode(sck, OUTPUT);
  pinMode(mosi, OUTPUT);

  /* Power down pin */
  pinMode(A0,INPUT_PULLUP);
  attachInterrupt(A0, powerdown, FALLING);

  SPI.begin();
  SPI.begin(SPI_MODE_MASTER); // SPI master
  SPI.setClockDivider(SPI_CLOCK_DIV4); // 60 MHz over 4 -> 15 MHz
  SPI.setBitOrder(MSBFIRST); // Bit 23 is first in buffer
  SPI.setDataMode(SPI_MODE1);  // According to github library

  analogWrite(fclk_pin, 127, fclk_freq); // Begin Bessel filter clock set at 50% duty cycle

  digitalWrite(enable_pin,LOW);
  initialization();
  Serial.begin();
  
  radio.begin();
  radio.openReadingPipe(0, address[0]);
  radio.setPALevel(RF24_PA_MIN);
  radio.setAutoAck(0,false);
  radio.startListening();

  //pitch_servo.attach(pitch_pin);
  azimuth_servo.attach(azimuth_pin);
  //pitch_servo.writeMicroseconds(pitch_servo_pos);
  azimuth_servo.writeMicroseconds(azimuth_servo_pos);
  delay(3000); //wait for servos to move into position
  
}

void loop() {
  // Set analog voltage X+, X-, Y+, Y- from center (analog_bias) always at 80 V
  // Max voltage is 157 so max analog voltage is 157 - if you go beyond 157, the DAC will set to 80 V and your code won't work.

  difX = 0; //Can be positive or negative
  difY = 0;
  incX = 0;
  incY = 0;
  setChannels(difX, difY);

  while(1) {
    while(! radio.available()); //wait for new communication
    radio.read(&radio_data, sizeof(radio_data[0])*2);
    p++;
    bufX[p] = difX;
    bufY[p] = difY;
    q = p+1;
    if (p>=BUF_SIZE) p=0;
    if (q>=BUF_SIZE) q=0;
    
    pulseWidth = pulseIn(WKP, HIGH); // Count how long the pulse is high in microseconds
    pulseWidth = pulseWidth/1000; // Get radial distance in meters

    incX = (bufX[p]-bufX[q])/BUF_SIZE;
    incY = (bufY[p]-bufY[q])/BUF_SIZE;
    difX += incX;
    difY += incY;
    difX += (double)(radio_data[0])/127.0 * inc;
    difY += (double)(radio_data[1])/127.0 * inc;

    az=difX*(2.0/pi*360.0/6*50); // volts to radians
    el=difY*(2.0/pi*360.0/6*50); // volts to radians
    h=pulseWidth*cos(el);
    z=pulseWidth*sin(el);
    //incX=atan(radio_data[0]/radio_data[1])/2.0/pi*360.0/6*50;
    //incY=atan(z/sqrt(radio_data[0]^2+radio_data[1]^2))/(2.0/pi*360.0/6*50); //radians to volts
    
    azimuth_servo_pos = azimuth_controller_update(difX);
    azimuth_write(azimuth_servo_pos);
    /*
    if (difX > 10){
      azimuth_servo_pos ++;
      azimuth_write(azimuth_servo_pos);
    }
    else if (difX < -10){
      azimuth_servo_pos --;
      azimuth_write(azimuth_servo_pos);
    }
    */
    
    setChannels(difX, difY);

    //Serial.print(radio_data[0]);
    //Serial.print(',');
    //Serial.println(radio_data[1]);
    
    serial_counter++;
    if (serial_counter > 50){
      Serial.print(difX);
      Serial.print(',');
      Serial.print(difY);
      Serial.print(';');
      Serial.println(azimuth_servo_pos);
      serial_counter = 0;
    }
  }
  powerdown(); //Always power down at the end to disable the MEMS output.. If you don't do this and disconnect the power you may break the MEMS
}

int azimuth_controller_update(double mems_pos) {
    const double ki = 0.0, kp=0.1, kd=0.0;
    static double err_i = 0;
    static double mems_last = 0;
    double err_p, err_d;

    err_i += mems_pos;
    err_p = mems_pos;
    err_d = mems_pos - mems_last;

    mems_last = mems_pos;

    return (int)(1500 + (err_i * ki) + (err_p * kp) + (err_d * kd));
}

void azimuth_write(int pos){
  if (pos < 1200 or pos > 1800) return;
  azimuth_servo.writeMicroseconds(pos);
}
void pitch_write(int pos){
  if (pos < 1600 or pos > 2000) return;
  pitch_servo.writeMicroseconds(pos);
}

// All functions for this to work
void initialization() {         //Initialization to set up DAC

    digitalWrite(ss,LOW);
    SPI.transfer((full_reset>>16) & 0xFF);  // bits 16-23
    SPI.transfer((full_reset>>8) & 0xFF);   // bits 8-15
    SPI.transfer(full_reset & 0xFF);        // bits 0-7
    digitalWrite(ss,HIGH);

    digitalWrite(ss,LOW);
    SPI.transfer((enable_internal_reference>>16) & 0xFF);
    SPI.transfer((enable_internal_reference>>8) & 0xFF);
    SPI.transfer(enable_internal_reference & 0xFF);
    digitalWrite(ss,HIGH);

    digitalWrite(ss,LOW);
    SPI.transfer((enable_all_dac_channels>>16) & 0xFF);
    SPI.transfer((enable_all_dac_channels>>8) & 0xFF);
    SPI.transfer(enable_all_dac_channels & 0xFF);
    digitalWrite(ss,HIGH);

    digitalWrite(ss,LOW);
    SPI.transfer((enable_software_ldac>>16) & 0xFF);
    SPI.transfer((enable_software_ldac>>8) & 0xFF);
    SPI.transfer(enable_software_ldac & 0xFF);
    digitalWrite(ss,HIGH);

    digitalWrite(enable_pin,HIGH); // Enable MEMS Output
    setChannels(0,0); // Set MEMS to bias offset of 80 V
}

void setChannels(double difX, double difY) {

  //check that the maximum voltage does not exceed 157 V

  double Xp = bias_voltage + difX;
  double Xm = bias_voltage - difX;
  double Yp = bias_voltage + difY;
  double Ym = bias_voltage - difY;

  if (Xp > max_voltage | Xm > max_voltage | Yp > max_voltage | Ym > max_voltage) {
    difX = 0; // If it exceeds 157 V, set the output to the bias voltage.
    difY = 0; // If it exceeds 157 V, set the output to the bias voltage.
  }

  //convert difX and difY to digital values
  double voltage[] = {Xp, Xm, Yp, Ym};

  digitalWrite(ss,HIGH); //pull out of idle

  for (int i = 0; i < 4; i++) {
    double analog_voltage = (voltage[i]*65535)/160 + 0.5; // Convert from voltage to digital value
    data = (int) analog_voltage;

    digitalWrite(ss,LOW);
    SPI.transfer(writecommand[i]); //Defined above to write to LDAC and write to DAC register on last channel
    SPI.transfer((data >> 8) & 0xFF);
    SPI.transfer(data & 0xFF);
    digitalWrite(ss,HIGH);
  }

  // DAC update all outputs simultaneously
  digitalWrite(ss,LOW);
  SPI.transfer(AD56X4_COMMAND_UPDATE_DAC_REGISTER | AD56X4_CHANNEL_ALL);
  SPI.transfer(0);
  SPI.transfer(0);
  digitalWrite(ss,HIGH);

  digitalWrite(ss,LOW); //idle for low current mode without powering down
}

void powerdown() {

  digitalWrite(enable_pin,LOW); //Disable MEMS output

  digitalWrite(ss,HIGH); //pull out of idle
  digitalWrite(ss,LOW);
  SPI.transfer((full_reset>>16) & 0xFF);  // bits 16-23
  SPI.transfer((full_reset>>8) & 0xFF);   // bits 8-15
  SPI.transfer(full_reset & 0xFF);        // bits 0-7
  digitalWrite(ss,HIGH);

  //Power down to idle
  digitalWrite(ss,LOW);
  SPI.transfer((disable_all_dac_channels>>16) & 0xFF);
  SPI.transfer((disable_all_dac_channels>>8) & 0xFF);
  SPI.transfer(disable_all_dac_channels & 0xFF);
  digitalWrite(ss,HIGH);
  //delay(1);
  digitalWrite(ss,LOW);
}

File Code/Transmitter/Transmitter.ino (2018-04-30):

/*
 * Adapted from code by Dejan Nedelkovski, www.HowToMechatronics.com
 * Library: TMRh20/RF24, https://github.com/tmrh20/RF24/
 */
#include <SPI.h>
#include "nRF24L01.h"
#include "particle-rf24.h"
#include "Particle.h"
#include "math.h"
SYSTEM_MODE(MANUAL);

/* Phton Pin Mapping 
 *  
 * Multiplexer pins:
 * BIT_16_PIN --> D0
 * BIT_8_PIN  --> D1
 * BIT_4_PIN  --> D2
 * BIT_2_PIN  --> D3
 * BIT_1_PIN  --> D4
 * OUT_PIN    --> D5
 * 
 * pins for radio:
 * radio (NRF24L01) --> Particle Photon
 * MOSI --> A5
 * MISO --> A4
 * SCK  --> A3
 * SS   --> A2
 * CE   --> D6
 * GND  --> GND
 * VCC  --> 3V3
 */

#define BIT_16_PIN D0 //MSB
#define BIT_8_PIN  D1
#define BIT_4_PIN  D2
#define BIT_2_PIN  D3
#define BIT_1_PIN  D4  //LSB
#define OUT_PIN    D5
#define X_MAX      9.25
#define Y_MAX      6.25
#define SIGNAL_PIN D7

const int ss          = A2; // SS or CSN for MEMS
const int sck         = A3; // (pin 6)
const int mosi        = A5; // (pin 4)
const int ce          = D6; // to set TX or RX modes for radio

/* This is the diode number .
 * The mux index is offset by 5. For example diode #3 --> 8 on mux
 *  | | <-- 5
 * 4  3   6  5      ^ This way up (such that array is at bottom right of board)
 *   8  7  10  9
 * 12 11  14 13
 *   16 15  18 17 
 * 20 19  22 21
 *   24 23  26 25
 */

/* dx and dy indexed by diode #, first three positions are not used
 * Diode # is shown above. 
 * dx and dy is distance from x and y axes in millimeters
 * origin is in center of photodiode array.
 */
const double dx[] = {-6.75, -1.75, 4.25, 9.25,
                     -9.25, -4.25, 1.75, 6.75,
                     -9.25, -4.25, 1.75, 6.75,
                     -6.75, -1.75, 4.25, 9.25,
                     -6.75, -1.75, 4.25, 9.25,
                     -9.25, -4.25, 1.75, 6.75 };
const double dy[] = {-1.25, -1.25, -1.25, -1.25,
                     1.25, 1.25, 1.25, 1.25,
                     -3.75, -3.75, -3.75, -3.75,
                     3.75, 3.75, 3.75, 3.75,
                     -6.25, -6.25, -6.25, -6.25,
                     6.25, 6.25, 6.25, 6.25};             
RF24 radio(ce, ss); // CE, CSN
byte addresses[][6] = {"1Node","2Node"};  
int    threshold, number_diodes_on;
int8_t data[2] = {0,0};
double dy_mean, dx_mean, dy_sum, dx_sum;

void setup() {
  Serial.begin(9600);
  radio.begin();
  radio.openWritingPipe(addresses[0]);
  radio.enableDynamicPayloads();
  radio.setPALevel(RF24_PA_MAX);
  radio.setAutoAck(0,false);
  radio.stopListening();

  pinMode(BIT_16_PIN, OUTPUT);
  pinMode(BIT_8_PIN,  OUTPUT);
  pinMode(BIT_4_PIN,  OUTPUT);
  pinMode(BIT_2_PIN,  OUTPUT);
  pinMode(BIT_1_PIN,  OUTPUT);
  pinMode(OUT_PIN,    INPUT_PULLUP);
  pinMode(SIGNAL_PIN, INPUT_PULLUP);
}

void loop() {
  dx_sum = 0;
  dy_sum = 0;
  number_diodes_on = 0;

  // iterate through mux
  for (int i=8 ; i < 32 ; i++){
    digitalWrite(BIT_1_PIN,  i & 1     );
    digitalWrite(BIT_2_PIN,  i & (1<<1));
    digitalWrite(BIT_4_PIN,  i & (1<<2));
    digitalWrite(BIT_8_PIN,  i & (1<<3));
    digitalWrite(BIT_16_PIN, i & (1<<4));
    if (digitalRead(OUT_PIN) == HIGH){
      dx_sum += dx[i];
      dy_sum += dy[i];
      number_diodes_on ++;
    }
  }
  if (number_diodes_on == 0){
    dx_mean = 0;
    dy_mean = 0;
  }
  else{
    dx_mean = dx_sum / number_diodes_on;
    dy_mean = dy_sum / number_diodes_on;
  }
  data[0] = round(dx_mean/X_MAX * 127);
  data[1] = round(dy_mean/Y_MAX * 127);
  //Serial.print(data[0]);
  //Serial.print(',');
  //Serial.println(data[1]);
  //delay(100);
  radio.write(&data, sizeof(data[0])*2);
}

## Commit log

2018-02-11 First Commit with base Transmitter Receiver Arduino Code
2018-03-24 Updated with servo code.
2018-03-24 I think this is a PID controller
2018-03-25 Added NRF pin out image
2018-03-27 Servo controller working
2018-03-28 cleaner coarse tracking (servo mechanism needs testing with a diff power supply)
2018-04-24 Add files via upload
    Some Lidar Stuff added
2018-04-29 Add PCBs
    [digikey_bom.csv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]
2018-04-29 Some of the Lidar stuff which isn't completely done added
2018-04-30 hardware report PCBs v1
2018-04-30 Added STL files for mechanical components.
    [back_plate.stl, camera_mount.stl, center_armature.stl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]
2018-05-03 Serial communication 'UDLR', servo movement deleted
2018-05-03 transformed dc values to milliseconds and write to serial
